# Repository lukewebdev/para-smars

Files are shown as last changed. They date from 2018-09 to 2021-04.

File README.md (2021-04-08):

# para-smars
Parametric library for generating SMARS robots. 

All credit for the original SMARS concept etc goes to creator of SMARS and the original robot - https://www.thingiverse.com/thing:2662828

This is a parametric effort, primarily aimed at the stepper version of SMARS, 
but the idea is to make a single code repository capable of generating all desirable variants of SMARS.

Benefits:

1. easy to adjust for quirks in individual 3d Printers
2. easy to adjust size to fit other battery options
3. Anyone can tweak without having to use proprietary software

Hopefully the biggest benefit to the community will be that people FORK this code and submit Pull Requests to improve it. 

SMARS right now consists of the original designs and many one-off tweaks. Because the project is not in code, it is not really
building on itself or improving overall.

Ideally, we could improve this so that one may simply choose their battery selection, and width/height etc and the robot model will generate itself.

To try out defaults, simply open
configuration_parameters.scad and change $fn=15 or something low to render it faster while developing.
Set iteme like batteries and preview to false:
show_batteries = true;
show_rear_system = true;
show_cable_management = true;
show_grooves = true;
show_chassis = true;
show_preview = false;
use_608_bearing = false; // should always be false...bearing variant is not working yet.

Then save and open
SMARS_LCV.scad in openscad and hit F5.  

Currently there is some clutter we need to clean up and some unused files.

A few videos of these robots in action:
https://www.youtube.com/watch?v=e3OiXQOx9ag

https://www.youtube.com/watch?v=ZqQueUTJkCA

https://www.youtube.com/watch?v=jl2UJ-XNMSg

Thingiverse page for this variant:
https://www.thingiverse.com/thing:3202688

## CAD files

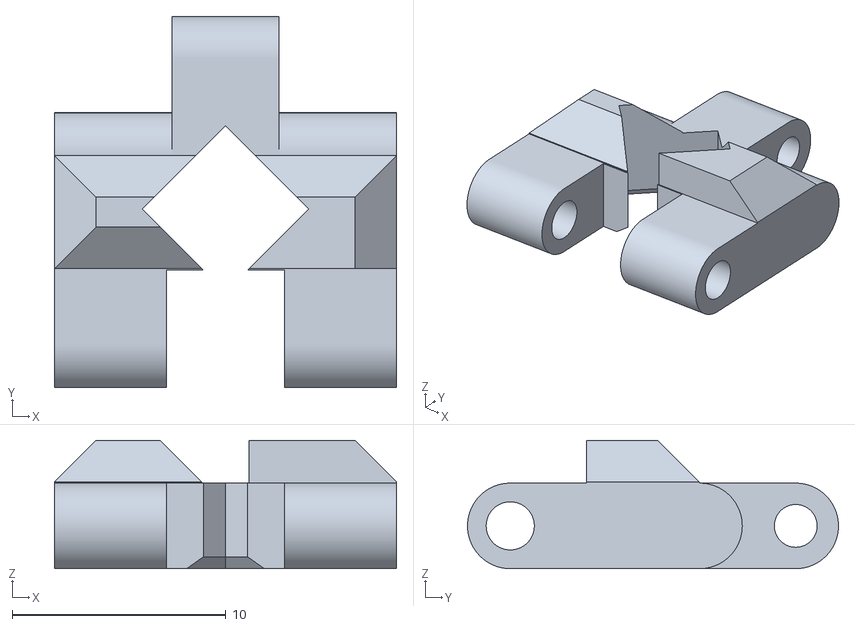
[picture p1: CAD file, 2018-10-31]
import/mechanical_track-orig-import-dont-print-use-modified.stl
16.0 x 17.4 x 6.00

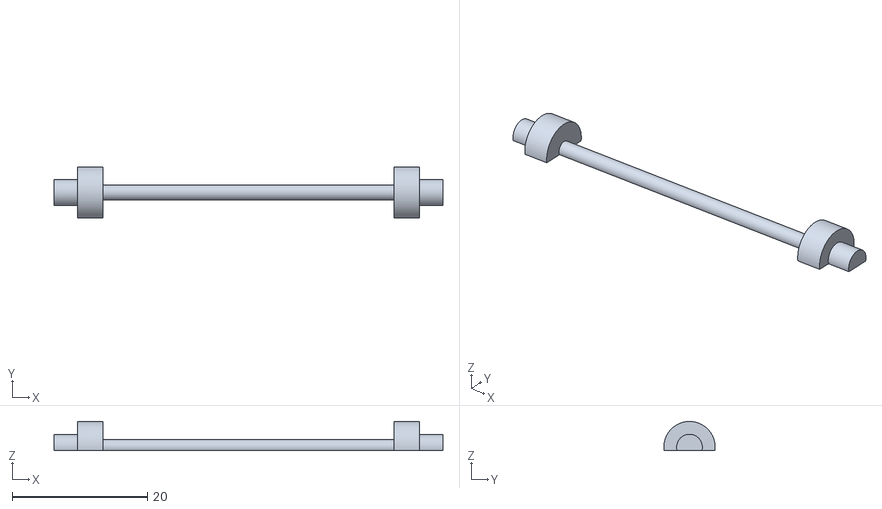
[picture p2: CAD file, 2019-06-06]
SMARS_LCV_Stepper_Lock_Pin.stl
57.5 x 7.60 x 4.30

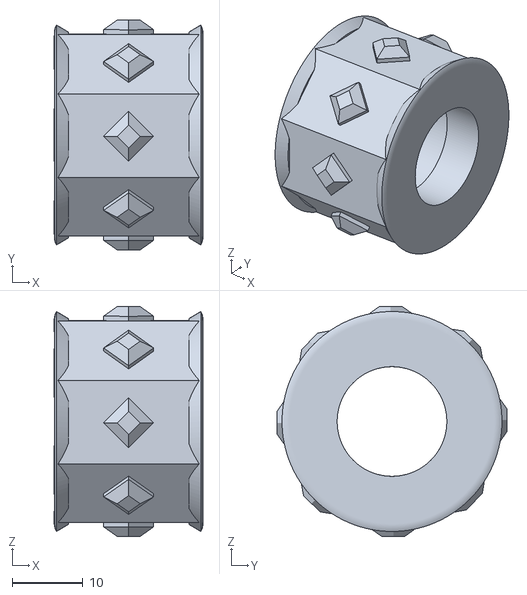
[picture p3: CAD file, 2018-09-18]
import/slave_wheel_SL.stl
21.0 x 32.5 x 32.5

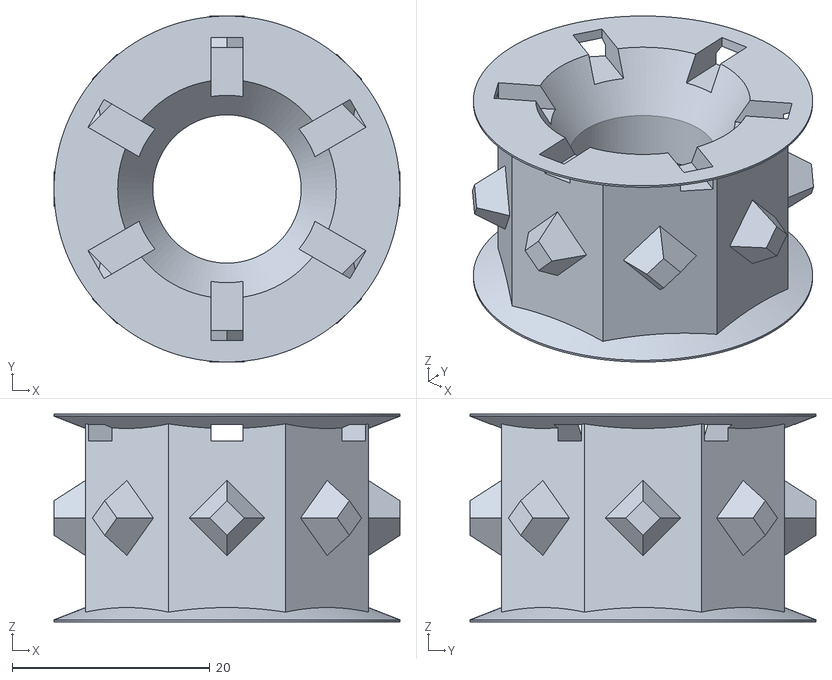
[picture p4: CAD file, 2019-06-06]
SMARS_Parametric_Slave_15.00mm_Wheel_16MM_axle_diff.stl
35.0 x 35.0 x 21.0

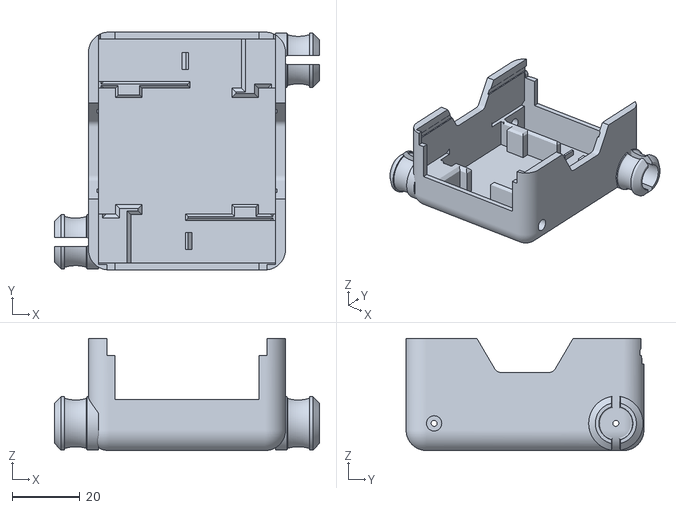
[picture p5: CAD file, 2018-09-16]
import/chassis_-SL.stl
78.0 x 70.0 x 33.0

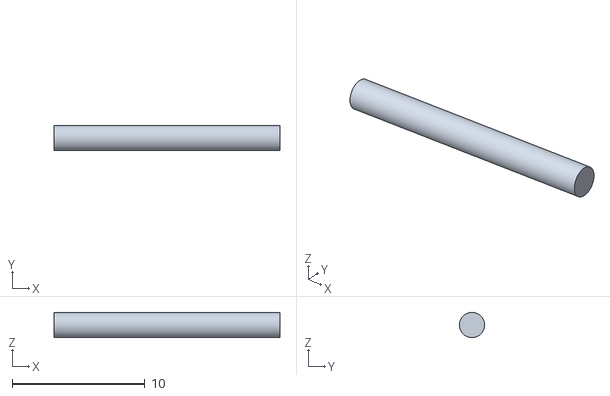
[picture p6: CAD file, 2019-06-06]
SMARS_track_tensioner_pin_1x_1.9mm.stl
17.0 x 1.90 x 1.90

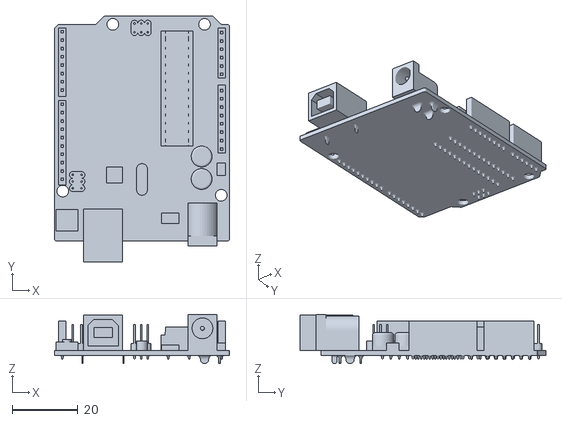
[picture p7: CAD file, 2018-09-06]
import/Arduino.stl
53.3 x 74.9 x 15.0

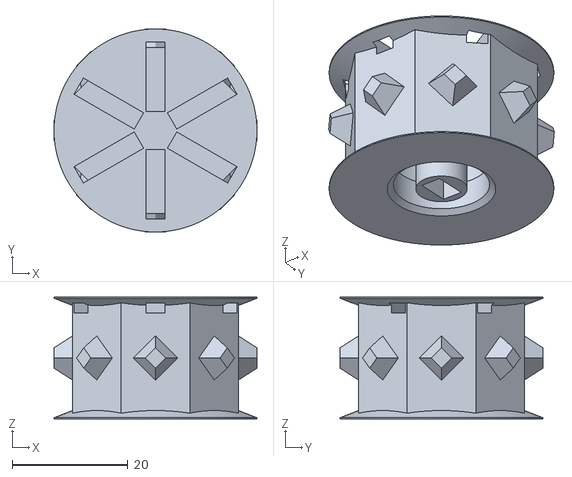
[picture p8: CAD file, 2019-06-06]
SMARS_Parametric_Master_15.00mm_Wheel_16MM_axle_diff.stl
35.0 x 35.0 x 21.0

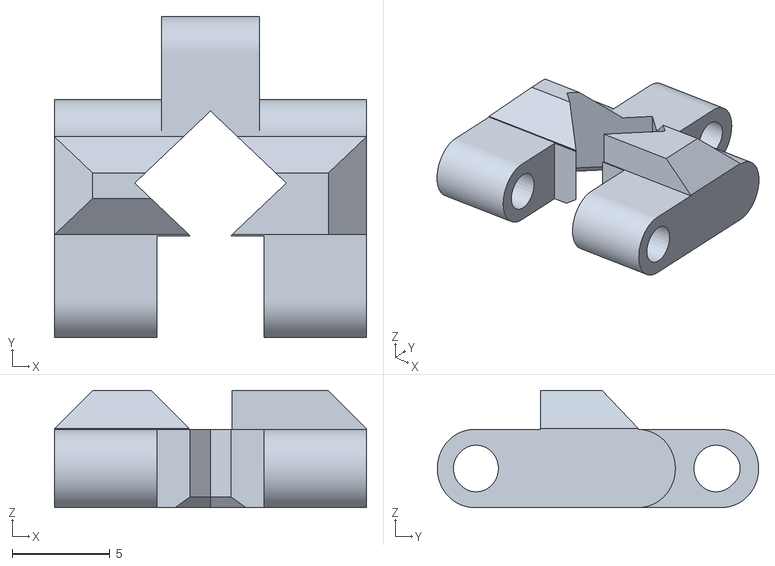
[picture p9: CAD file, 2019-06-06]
SMARS_LCV_mechanical_track_expansion-95-percent-Y.stl
16.0 x 16.5 x 6.00

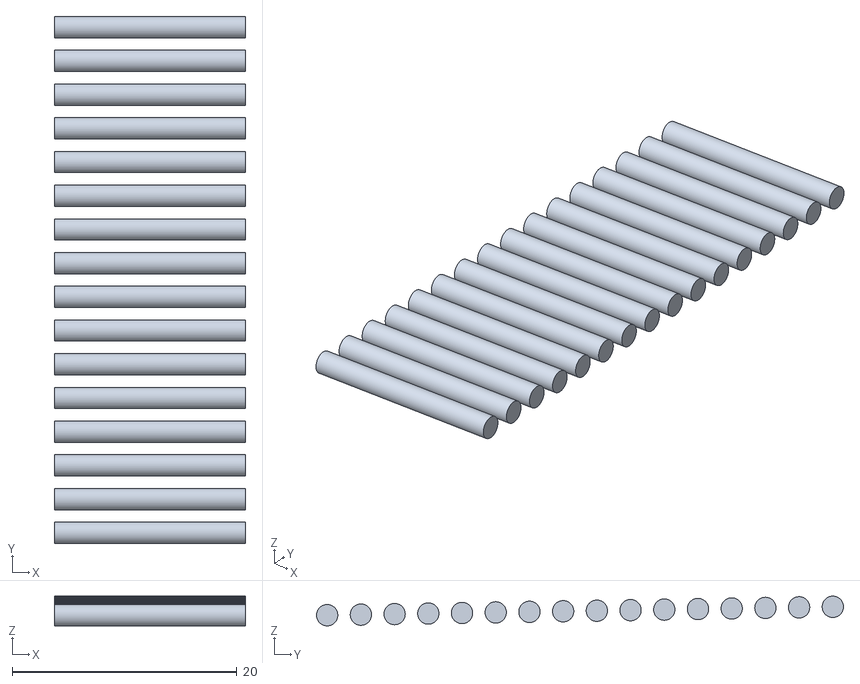
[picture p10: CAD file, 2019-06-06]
SMARS_track_tensioner_pins_16x1.9mm.stl
17.0 x 46.9 x 2.65

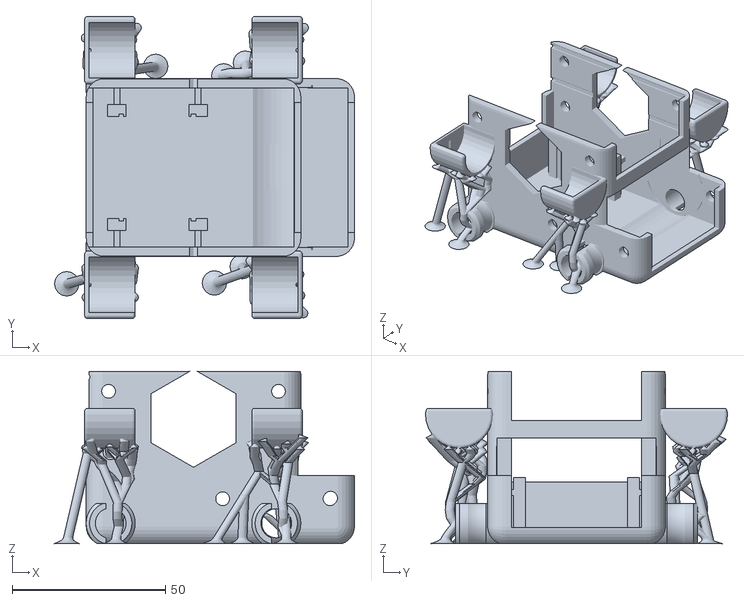
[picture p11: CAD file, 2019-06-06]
SMARS_LCV_TREES.stl
97.8 x 98.5 x 56.1

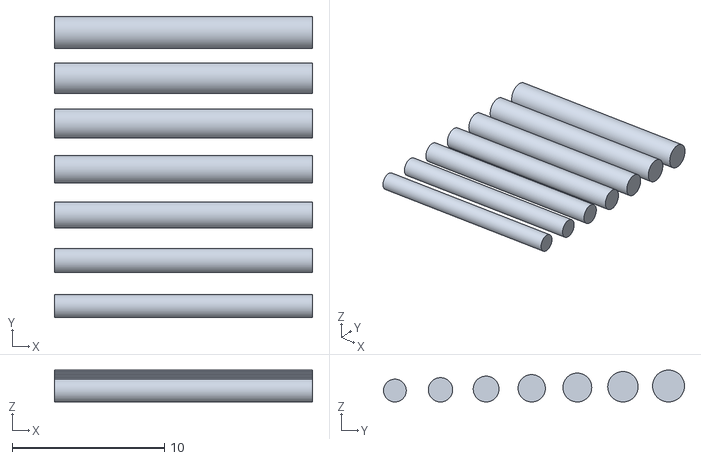
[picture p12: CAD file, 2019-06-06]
SMARS_track_tensioner_pins.stl
17.0 x 19.8 x 2.10

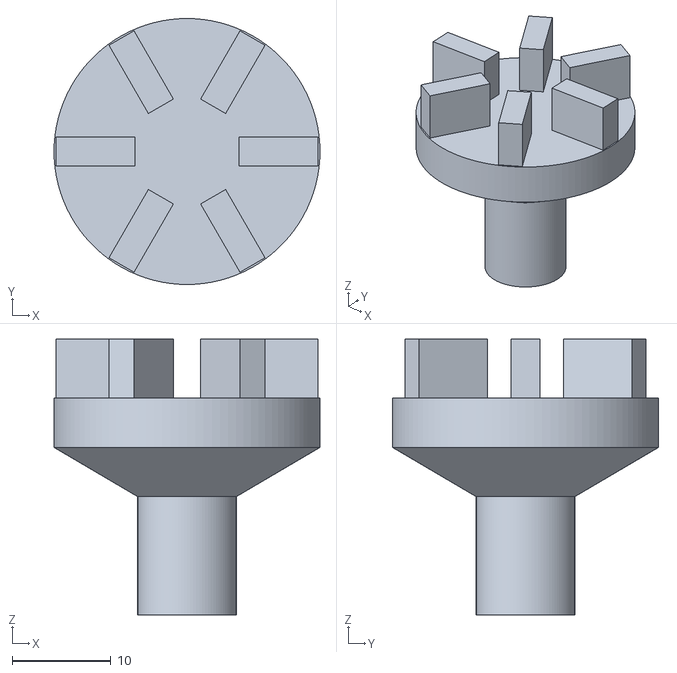
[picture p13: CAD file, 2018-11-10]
SMARS_Drill_Wheel_Spinner_break_in_tool.stl
27.0 x 27.0 x 28.0

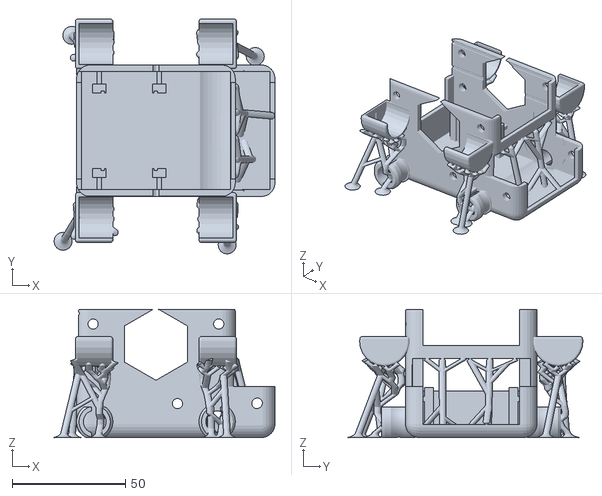
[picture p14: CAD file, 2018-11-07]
SMARS_LCV_clone_TREES_overhang_support.stl
97.5 x 103.6 x 56.5

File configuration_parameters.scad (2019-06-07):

$fa=1;
$fs=1.5;
$fn = 15;//dev 15, to print at least 25
fn=$fn;

show_batteries = false;
show_rear_system = true;
show_cable_management = false;
show_grooves = true;
show_chassis = true;
show_preview = false;
use_608_bearing = false; // should always be false...bearing variant is not working yet.


//PCB thickness
groove_d = 1.5;


//stepper driver config
stepper_driver_h = 32;
stepper_driver_w = 34.65;
stepper_driver_t = 1.5;
stepper_driver_front_offset = 2.2;//make room for tool modules
stepper_motor_max_d = 35;
stepper_motor_main_d = 28;
stepper_hole_mount_d  = 4.5;
stepper_z_nudge = -1;//move entire stepper motor accommodations up or down
stepper_x_nudge = .5;

//WHEEL CONF
axle_d = 16;
axle_h = 15;
wheel_w = 21;
wheel_d = 31;
wheel_width_beyond_sl_axle = 12;
wheel_d = 31;
sl_axle_ledge=.5;

//BEARING (if applicable)
bearing_608_axle_d = 8;//608 bearing has 8mm inner diameter
bearing_chassis_offset = 10;
bearing_608_axle_h = axle_h + bearing_chassis_offset;

//Print Tweaks
//manual_brim = true;
pyramid_h = 2;//pyramid tread height
rim_w = 1; //thickness of rim on either side of wheel (keeps tracks from sliding off if track is loose

//arduino and module groove config
arduino_pcb_thickness = 1.7;
arduino_width = 53;
arduino_length = 66;

//BATTERY CONF, shown below 18650 battery
battery_z = 41.5;
battery_tilt=0;
battery_y_offset = 6.25;

//CHASSIS CONF
rear_wheel_buffer = 11;
wall_width = 3; // how thick are the walls of the chassis


//MODULE HOLDER CONFIG
module_difference_x=42.5;
module_difference_y=4;
module_difference_z=15;

radius = 5;//curve of the chassis box. 0 is square. 5 is default/normal....not more than ten or need to adjust stepper mount hub code
//chassis width, height, length
chassis_w =  58; 
chassis_h =56.5+ radius;
chassis_l = 70;

/*
radius = 5;//not more than ten or need to adjust stepper mount hub code
chassis_w =  75; // 40 is two stepper motors
chassis_h =58+ radius;
chassis_l = 100;
*/

roof_offset = 40; // just how high to show roof separate from chassis
front_back_hex_d=35;
side_hex_d=32; // bix side polygon for hookup/jumper wires

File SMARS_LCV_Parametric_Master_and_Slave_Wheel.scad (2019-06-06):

/* openscad code by Luke Meier, contributed to SMARS project which was created by Kevin Thomas*/


$fn = 100;


 //THIS IS A WORkING LARGER SLAVE WHEEL  smooth
//wheel(axle_d = 15, wheel_w=20.6, wheel_d = 32, pyramid_h = 3.5, pyramid_d=8, pyramid_d2=3.5, rim_w=.2, rim_d = 35, do_pyramids =false);


//slave wheel geared, larger than master to take up slack in track.
wheel(axle_d = 15, wheel_w=20.6, wheel_d = 31, pyramid_h = 3.5, pyramid_d=8, pyramid_d2=3.5, rim_w=.2, rim_d = 35, do_pyramids =true, fn = 8);

//sample master  - for stepper variant
//wheel(axle_d = 15, wheel_w=20.6, wheel_d = 31, pyramid_h = 3.5, pyramid_d=8, pyramid_d2=3.5, rim_w=.2, rim_d = 35, do_pyramids =true, fn = 8, slave=false);

//tool for breaking in wheel (use vaseline on axle and pin the wheel after track is installed until plastic anneals and smooths our print imperfections)
//wheel_spinner_drill_attachment();
module wheel(axle_d = 15, wheel_w=20.6, wheel_d = 32, pyramid_h = 2, rim_w=.2, rim_d = 35, fn = $fn, do_pyramids = false, slave=true, SL_axle_h=6){
    
    //main wheel
    rotate([180,0,90])
    union(){
        difference(){

            union(){
                rotate([0,0,022.5])
                cylinder(d=wheel_d, h=wheel_w, center=true, $fn = fn);//make $fn = 8 for original
                //rims
                color("purple")
                hull(){
                    translate([0,0,wheel_w/2 + rim_w/2])
                    cylinder(d=rim_d, h = rim_w, center=true);
                    
                    color("red")
                    translate([0,0,wheel_w/2 + rim_w/2 - 1.25])
                    cylinder(d=wheel_d-2.4, h = rim_w, center=true);
                }
                color("purple")                
                hull(){
                    translate([0,0,-wheel_w/2 +- rim_w/2])
                    cylinder(d=rim_d, h = rim_w, center=true);              
                    
                    color("red")
                    translate([0,0,-wheel_w/2 + -rim_w/2 + 1.25])
                    cylinder(d=wheel_d-2.4, h = rim_w, center=true);                    
                }
            }
            if(slave==true){
                cylinder(d=axle_d,h=wheel_w*2 + rim_w*2,center=true);
            }else{

                translate([0,0,wheel_w/4 + rim_w +1])
                cylinder(d=axle_d,h=wheel_w/2 +7 + rim_w*2,center=true);
            }

            //ball difference for ball tip of axle
            translate([0,0,2.5])   
            rotate([0,180,0]) 

            SL_axle_diff(axle_d = 16, SL_axle_h = SL_axle_h);
            

 


            if(slave==true){

                 for (i = [1 : 6]){
                    color("yellow")
                    rotate([60*i,90,0])
                    translate([wheel_w/2,0,wheel_w/2 -5])    
                   // rotate([0,45,0])
                    translate([0,0,4])
                    cube([5, (2*(wheel_d/2)*3.14)/30, 12], center=true);
                }
                
               //wheel chamfer
                translate([0,0,-wheel_w/2])
                cylinder(d=wheel_d*1.25, d2=5, h=wheel_w*1.4, center=true);                

                translate([0,0,-wheel_w/2 * rim_w*2 + 15.5])
                mirror([0,0,1])        
                cylinder(d=wheel_d*1.2, d2=1, h=wheel_w*.7, center=true);                   
                            
            }else{
               for (i = [1 : 6]){
                    color("yellow")
                    rotate([60*i,90,0])
                    translate([wheel_w/2,0,wheel_w/2 -5])    
                   // rotate([0,45,0])
                    translate([0,0,4])
                    cube([5, (2*(wheel_d/2)*3.14)/30, 12], center=true);
                }
             
                

                translate([0,0,-wheel_w/2 * rim_w*2 + 15.5])
                mirror([0,0,1])        
                cylinder(d=wheel_d*1.2, d2=1, h=wheel_w*.7, center=true);                   
                
            }

            
            
                   

        }
      
        //tread
        if(do_pyramids == true){
            for (i = [1 : 8]){
                color("red")
                rotate([45*i,90,0])
                translate([0,0,wheel_d/2-1.5])    
                cylinder(d=pyramid_d,d2=pyramid_d2,h=pyramid_h,$fn=4);
            } 
        }
        
        
        if(slave != true){
            difference(){
                //shaft that goes into wheel axle
                translate([0,0,0])
                cylinder(d=8, h=wheel_w+ rim_w*2, center=true);
                
                //take off outter part of inner cylinder to clear outter chamfer
                translate([0,0,-(wheel_w + rim_w*2)/2 +3])
                cylinder(d=18, h=6, center=true);                
                
                //stepper shaft slot
                color("red")
                translate([0,0, +20.6/2 +.2])
                cube([5.5,3.5,29],center=true); 
                
            }
        }
        //wheel chamfer to account for first layer print being wider

        

    }
}
//rotate([180,0,90])

module bearing_retainer(){

}
module bearing_608_difference(wheel_w=21, rim_w=1){
    color("red")
    translate([0,0,wheel_w/2+rim_w - 17/4])
        cylinder(d=22, h=17, center=true);//7mm + 1 for extra depth into wheel, must correspond to axle configuration
}

module pyramids(pyramid_h=2, wheel_w = wheel_w, wheel_d = wheel_d,pyramid_d = pyramid_d, pyramid_d2 = pyramid_d2){
  
}
module wheel_slave_original(){
    rotate([90,90,0])
    translate([35,-26.75,-8.2])

    color("green")
    import("import/slave_wheel_SL.stl");
}


module SL_axle_diff(axle_d = 15){//keep in sync with main chassis axle code!
    axle_h=15;

   // scale(v = [1.0625,1.0625,1])
    difference(){
        color("pink") 
        hollowCylinder(d=axle_d+1, h=SL_axle_h, ww=3, center=true);
        translate([0,0,7])
        color("red")
        torus(d1=axle_d-5, d2=axle_d, fill=false, center=true);               
    }

}



module wheel_spinner_drill_attachment(axle_d = 15, wheel_w=20.6, wheel_d = 32, pyramid_h = 2, rim_w=.2, rim_d = 35, fn = $fn, do_pyramids = false, slave=true, SL_axle_h=6){
    translate([0,0,0])   
    rotate([0,180,0]) 

    union(){
        for (i = [1 : 6]){
            color("yellow")
            rotate([60*i,90,0])
            translate([0,0,wheel_w/2 -5])    
            // rotate([0,45,0])
            translate([0,0,4])
            cube([11, (2*(wheel_d/2)*2.75)/30, 8], center=true);
        }
        translate([0,0,3])
        cylinder(h=5, d=27,center=true);

        translate([0,0,12.5])
        cylinder(h=20, d=10, center=true);
        
        translate([0,0,8])
        cylinder(h=5, d1=27, d2=10, center=true);        
    }

}

module hollowCylinder(d=5, h=10, ww=1, $fn=140)
{
	difference()
	{
		cylinder(d=d, h=h, center=true);
		translate([0, 0, -0.1]) { cylinder(d=d-(ww*2), h=h+0.2, center=true); }
	}
}


module torus(d1=10, d2=2, $fn=140)
{
	rotate_extrude()
	{
		translate([(d1/2)+(d2/2), 0, 0])
		{
			circle(d=d2);
		}
	}

}

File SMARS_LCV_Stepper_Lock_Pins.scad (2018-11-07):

difference(){
    union(){
        difference(){
            basicpin();
                //remove center
             rotate([0,90,0])
             cylinder(h = 43, r1 = 4, r2 = 4, center = true, $fn=100);
                


        }
        //main shaft
        rotate([0,90,0])
        cylinder(h = 50, r1 = 1.1, r2 = 1.1, center = true, $fn=100);

    }
    //flat bottom
    translate([0,0,-5.5])
    rotate([0,90,0])
    cube([10,12,60],center=true);    
}



//stoppers
module stop(){
    cylinder(h = 4, r1 = 3.8, r2 = 3.8, center = true, $fn=100);
}

module basicpin(){
 rotate([0,90,0])
    difference(){
        union(){
            
            //main key shaft
            cylinder(h = 57.5, r1 = 1.9, r2 = 1.9, center = true, $fn=100);
            //cylinder(h = 52, r1 = 2.3, r2 = 2.3, center = true, $fn=100);

            //stoppers
            translate([0,0,23.25])
            stop();
            //this was 23
            translate([0,0,-23.25])
            stop();
        }

        

    }   
}

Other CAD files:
SMARS_LCV_mechanical_track_expansion-103-percent-Y.stl
SMARS_Parametric_Master_15.00mm_Wheel.stl
SMARS_LCV_mechanical_track_expansion-102-percent-Y.stl
SMARS_Parametric_Slave_15.00mm_Wheel.stl
SMARS_track_tensioner_pins.scad
18650_tensioner.scad
SMARS_LCV.scad
SMARS_LCV_SCAD_FINAL3_with_tree_supports.stl
SMARS_LCV_mechanical_track_expansion.scad
laser_cut_wheel.scad
smars_lcv_tree_support.stl
use/Nut_Job.scad
use/StepMotor_28BYJ-48.scad
use/openscad/SMARS_608_Bearing_Wheel.scad
use/openscad/dome.scad
use/openscad/dovetailJoint.scad
use/openscad/hollowCylinder.scad
use/openscad/legacy/common.scad
use/openscad/legacy/espMount.scad
use/openscad/legacy/joinerBox.scad
use/openscad/legacy/joinerCylinder.scad
use/openscad/legacy/legacy-common.scad
use/openscad/legacy/nailsAndScrews.scad
use/openscad/nails.scad
use/openscad/pcbMount.scad
use/openscad/pinConnector.scad
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

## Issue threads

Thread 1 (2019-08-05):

Missing referenced library morphology.scad

mjparme, 2019-08-05:
The file `laser_cut_wheel.scad` references: `use </Users/luke/Documents/2D-3D-FlowmBot/use/scad-utils/morphology.scad>`. The `morphology.scad` file is nowhere in the source. Could you include this file? (it apparently contains the `outset` module).

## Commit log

2018-09-05 sMARS LC amphibious?
    [SMARS_LCSL_CHASSIS_AXLES_fixed.stl, SMARS_LCV_SCAD.scad, common.scad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]
2018-09-05 improved axle handling
    [SMARS_LCV_SCAD.scad]
2018-09-05 before changing battery orientation plan
    [SMARS_LCSL_CHASSIS_AXLES_fixed.stl, SMARS_LCV_SCAD.scad, StepMotor_28BYJ-48.scad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]
2018-09-06 basic smars stepper
    [SMARS_LCV_SCAD.scad]
2018-09-06 amphibioius smars 1.01
    [Arduino.stl, SMARS_LCV_SCAD.scad]
2018-09-06 fixed amphibious roof shape
    [SMARS_LCV_SCAD.scad]
2018-09-06 1st print
    [SMARS_LCV_SCAD.scad, SMARS_LCV_SCAD.stl]
2018-09-16 from scratch smars
    [SMARS_LCV_SCAD.scad, SMARS_LCV_SCAD.stl, SMARS_LCV_SCAD_clone.scad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]
2018-09-16 rear slot top slant needs to be fixed
    [SMARS_LCV_SCAD_clone.scad]
2018-09-17 updated version 2 issues such as axle, stepper spacing, etc.
    [SMARS_LCV_SCAD_clone.scad]
2018-09-17 fixes for battery holder etc
    [SMARS_LCV_SCAD_clone.scad, smars_18650_integral.scad, smars_18650_single_holder.scad]
2018-09-18 starting on wheel etc
    [SMARS_608_Bearing_Wheel.scad, SMARS_LCV_SCAD_clone.scad, slave_wheel_SL.stl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]
2018-09-19 refined mk1
    [SMARS_608_Bearing_Wheel.scad, SMARS_LCV_SCAD_clone.scad, wheel.scad]
2018-09-19 with top tool attachment
    [SMARS_LCV_SCAD_clone.scad]
2018-09-20 remove preview parts
    [SMARS_LCV_SCAD_clone.scad]
2018-09-21 final rounded-rear model
    [SMARS_608_Bearing_Wheel.scad, SMARS_LCV_SCAD_clone.scad]
2018-09-21 final-final SMARS-LCV SL Chassis Design
    [608_axle_test.stl, 608_axle_test_2.stl, SMARS_LCV_SCAD_FINAL3_with_tree_supports.stl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]
2018-09-27 updated smars master hub stepper wheel
    [SMARS_608_Bearing_Wheel.scad, SMARS_LCV_SCAD_FINAL4_with_tree_supports.stl, SMARS_LCV_SCAD_clone.scad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]
2018-09-30 wheel refinement, looser shaft attachment to avoid shaft pushing on master wheel and causing binding when samson pins are attached
    [SMARS_LCV_SCAD_clone.scad, SMARS_Parametric_Master_15.00mm_Wheel.stl, SMARS_Parametric_Master_Wheel.stl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]
2018-10-31 updated improvements to reduce post-processing on wheel axle shafts etc.
    [608_axle_test.stl, 608_axle_test_2.stl, LadySMARSv3.stl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]
2018-11-07 final print design for class 2018-2019
    [SMARS_Drill_Wheel_Spinner_break_in_tool.stl, SMARS_LCV_SCAD_clone.scad, SMARS_LCV_clone_TREES.stl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]
2018-11-07 clean up old files, reorganize
    [LadySMARSv3.stl, SMARSModConnector.stl, SMARS_LCV.scad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]
2018-11-07 remove extraneous files
    [SMARS_LCV_SCAD_clone.scad, SMARS_LCV_SLAVE_WHEEL_V2.scad, SMARS_LCV_Stepper_Lock_Pins.scad]
2018-11-07 add configuration file notes
    [SMARS_LCV.scad, configuration_parameters.scad]
2018-11-07 removed other parts
    [LadySMARSv3.stl, SMARSModConnector.stl, SMARS_LCV_mechanical_track_expansion.stl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]
2019-06-06 add STLs and updated code.
    [18650_tensioner.scad, Nut_Job.scad, SMARS_LCV.scad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]
2019-06-07 update to more sensible default dev/faster render parameters
    [configuration_parameters.scad]
